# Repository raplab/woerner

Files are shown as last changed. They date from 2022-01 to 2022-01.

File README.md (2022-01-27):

# Wörner - Conventional Drill 
drilling and tapping machine control-code for a custom made electrical cabinet as upgrade of an old drill/milling-machine.
The controllino maxi automation acts as an SPS controlling various inputs and states - e.g. drilling, tapping and e-stop-mode.

## Requirements
- Controllino MAXI Automation https://www.controllino.com/product/controllino-maxi-automation/
- Eaton DE-1 (vfd) for motor control

# Documentation

## PIN Out
| Controllino Pin | Variable Name |  Input or Output |Cabinet Pin | Notes | 
|---|---|---|---|---|
| AI0 |  estop_pin |  INPUT |  - | read e-stop state, HIGH=ESTOP |
| AI1 |  contactor_pin | INPUT  | -  | read contactor state to determin if VFD has power  |
| AI2 |  vfd_state_pin |  INPUT | -  | read VFD state |
| AI3 |  cp_on_pin | INPUT  | -  |  spindle on |
| AI4 |  cp_off_pin | INPUT  | -  |  spindle off |
| AI5 |  cp_cw_pin | INPUT  | -  |  spindle direction clockwise |
| AI6 |  cp_ccw_pin | INPUT  | -  | spindle direction counterclockwise  |
| AI7 |  cp_mode_pin |  INPUT | -  | select between drilling or tapping mode  |
| AI9 |  w_topswitch_pin | INPUT  | -  | top switch for tapping mode (reverse spindle direction on HIGH) |
| AI10  |  w_bottomswitch_pin | INPUT  | -  |  bottom switch for tapping mode (reverse spindle direction on HIGH) |
| AI11  |  w_footswitch_pin |  INPUT | -  | foot switch for tapping mode (reverse spindle direction on HIGH)  |
| AI12  |  cp_speed_pin | INPUT  | -  |  analog input from 4.7k pot (0,1025) mapped to (0,255) vfd_speed_pin |
| AI13  |  tap_speed_pin | INPUT  | -  |  analog input from 4.7k pot (0,1025) mapped to (0,255) tap_speed_pin |
| DO0 |  cp_indicator_pin | OUTPUT  | -  | turn led on if spindle is on  |
| DO1 |  vfd_cw_pin | OUTPUT | -  |  turn spindle on in clockwise direction |
| DO2 |  vfd_ccw_pin | OUTPUT  | -  |  turn spindle on in counterclockwise direction  |
| DO3 |  ec_reset_pin | OUTPUT | -  |  led - high if reset is required |
| AO0 |  vfd_speed_pin | ANALOG OUTPUT  | | Analog out from 0-10V to control motor speed  |

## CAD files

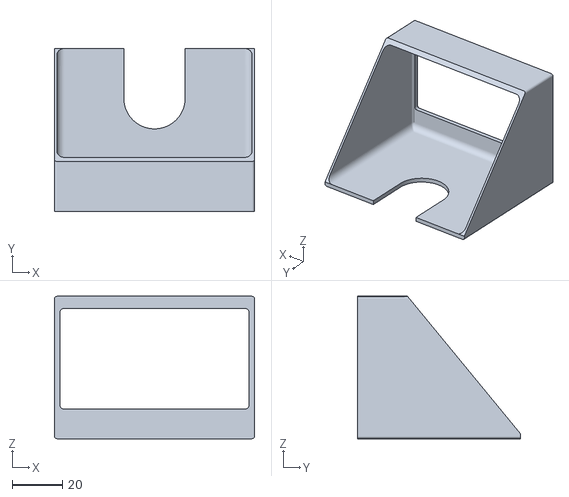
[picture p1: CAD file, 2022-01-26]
3d_prints/Wörner_Tacho_Housing.stl
80.0 x 65.2 x 57.0

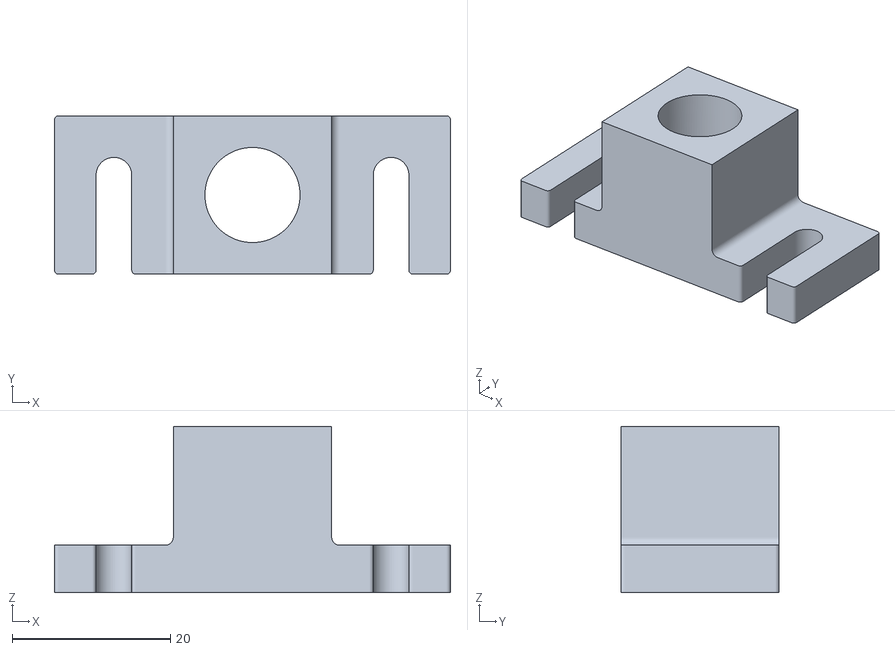
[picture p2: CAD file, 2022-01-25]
3d_prints/Sensor_Halter.stl
50.0 x 20.0 x 21.0

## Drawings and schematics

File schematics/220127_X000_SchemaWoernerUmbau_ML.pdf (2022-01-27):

-1F3

L3

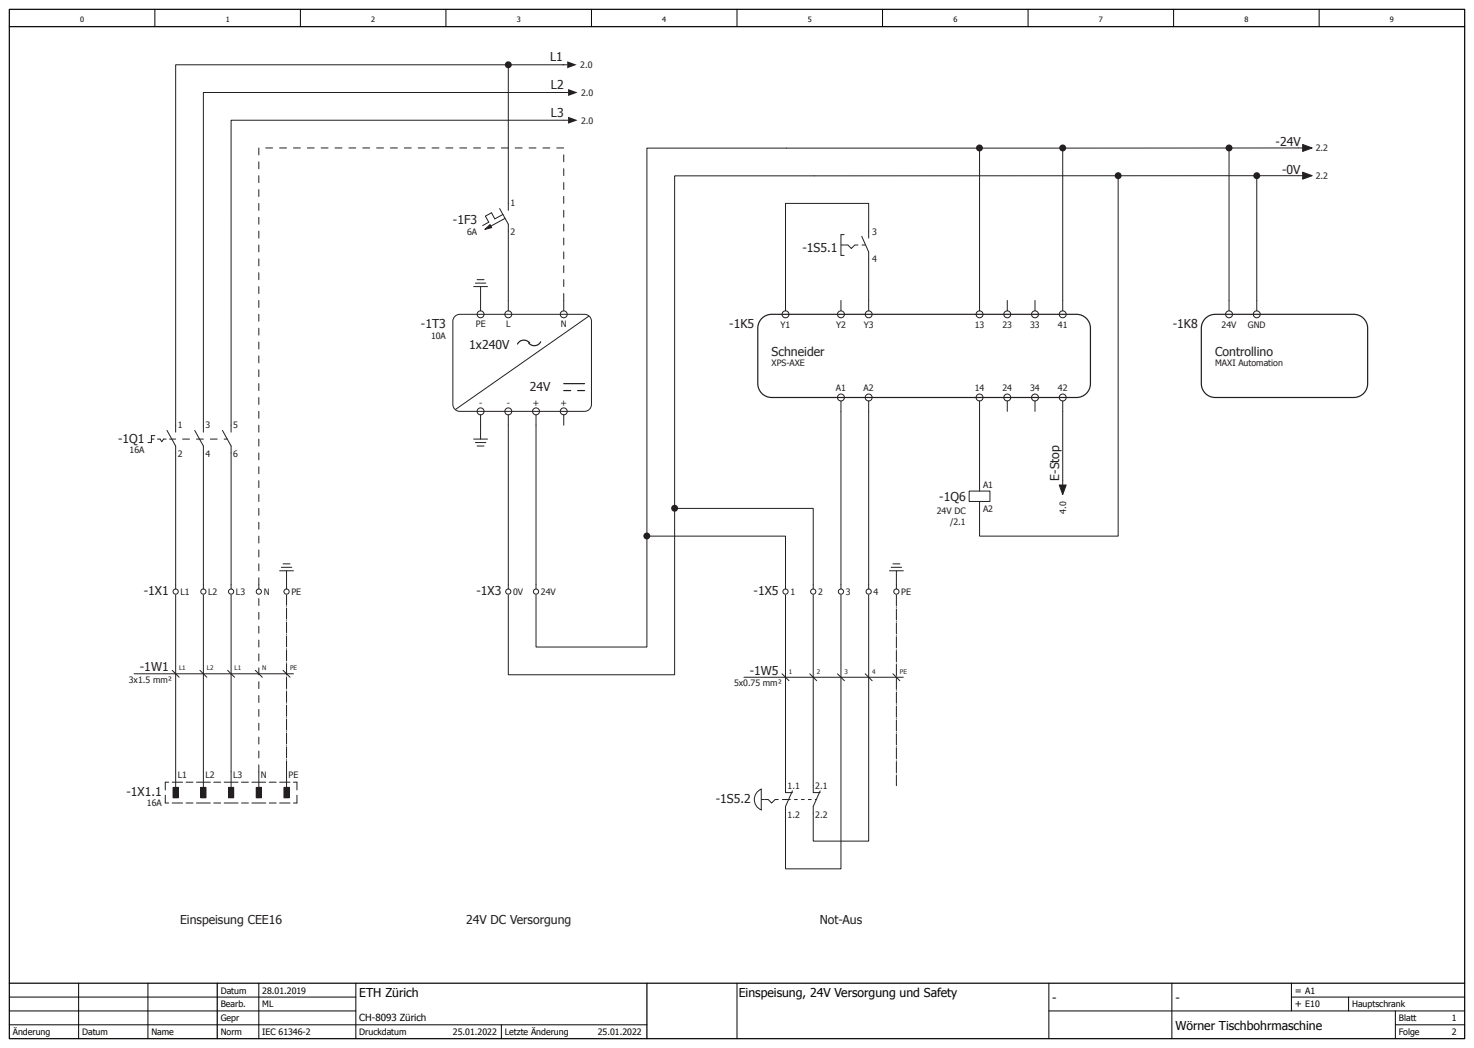
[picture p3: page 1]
Blatt Folge; Bearb.; Norm; Datum; Änderung; Letzte Änderung; Gepr; Druckdatum; Name; Hauptschrank; ETH Zürich; IEC 61346-2; Wörner Tischbohrmaschine CH-8093 Zürich; Schneider; XPS-AXE; 3x1.5 mm²; 5x0.75 mm²; Einspeisung CEE16; 24V DC Versorgung; Not-Aus; E-Stop 4.0; Controllino; MAXI Automation; GND

Einspeisung, 24V Versorgung und Safety

-2F1

-0V 1.8

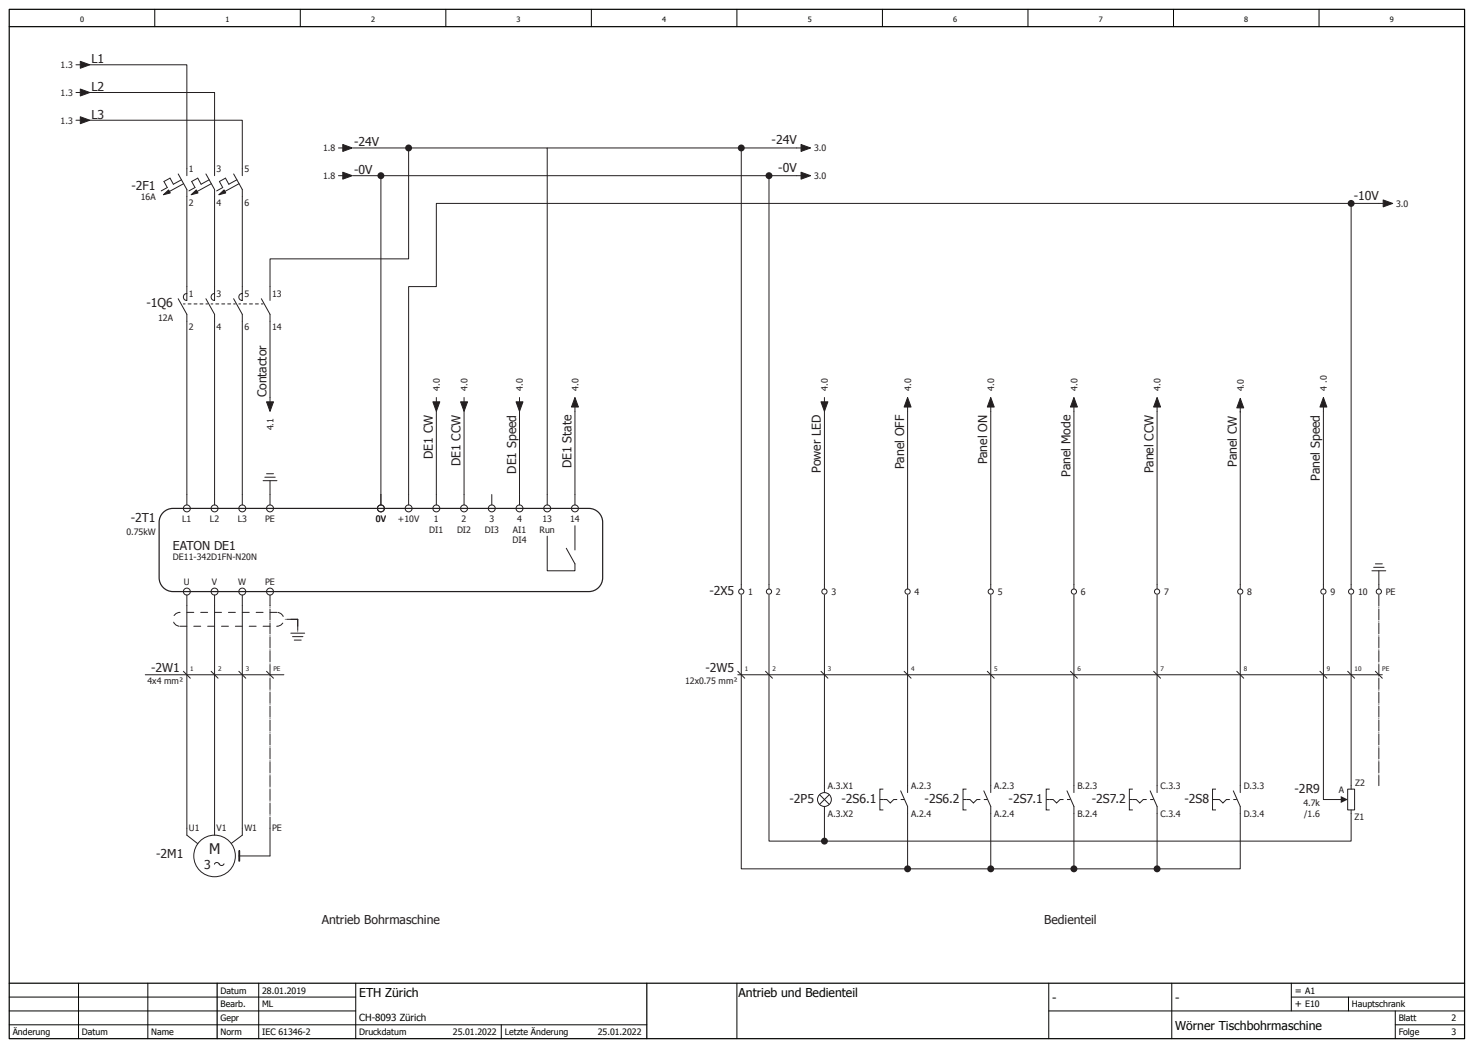
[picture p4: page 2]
EATON DE1; Run; 4x4 mm²; Antrieb Bohrmaschine; Bedienteil; DE1 CCW; DE1 Speed 4.0; DE1 State; Contactor; 12x0.75 mm²; 10 Panel OFF ⁴.0 Power LED ⁴.0; Panel ON ⁴.0; Panel Mode ⁴.0; Panel CCW ⁴.0; Panel CW ⁴.0; Panel Speed 4 .0

Antrieb und Bedienteil

-24V 2.5

-0V 2.5

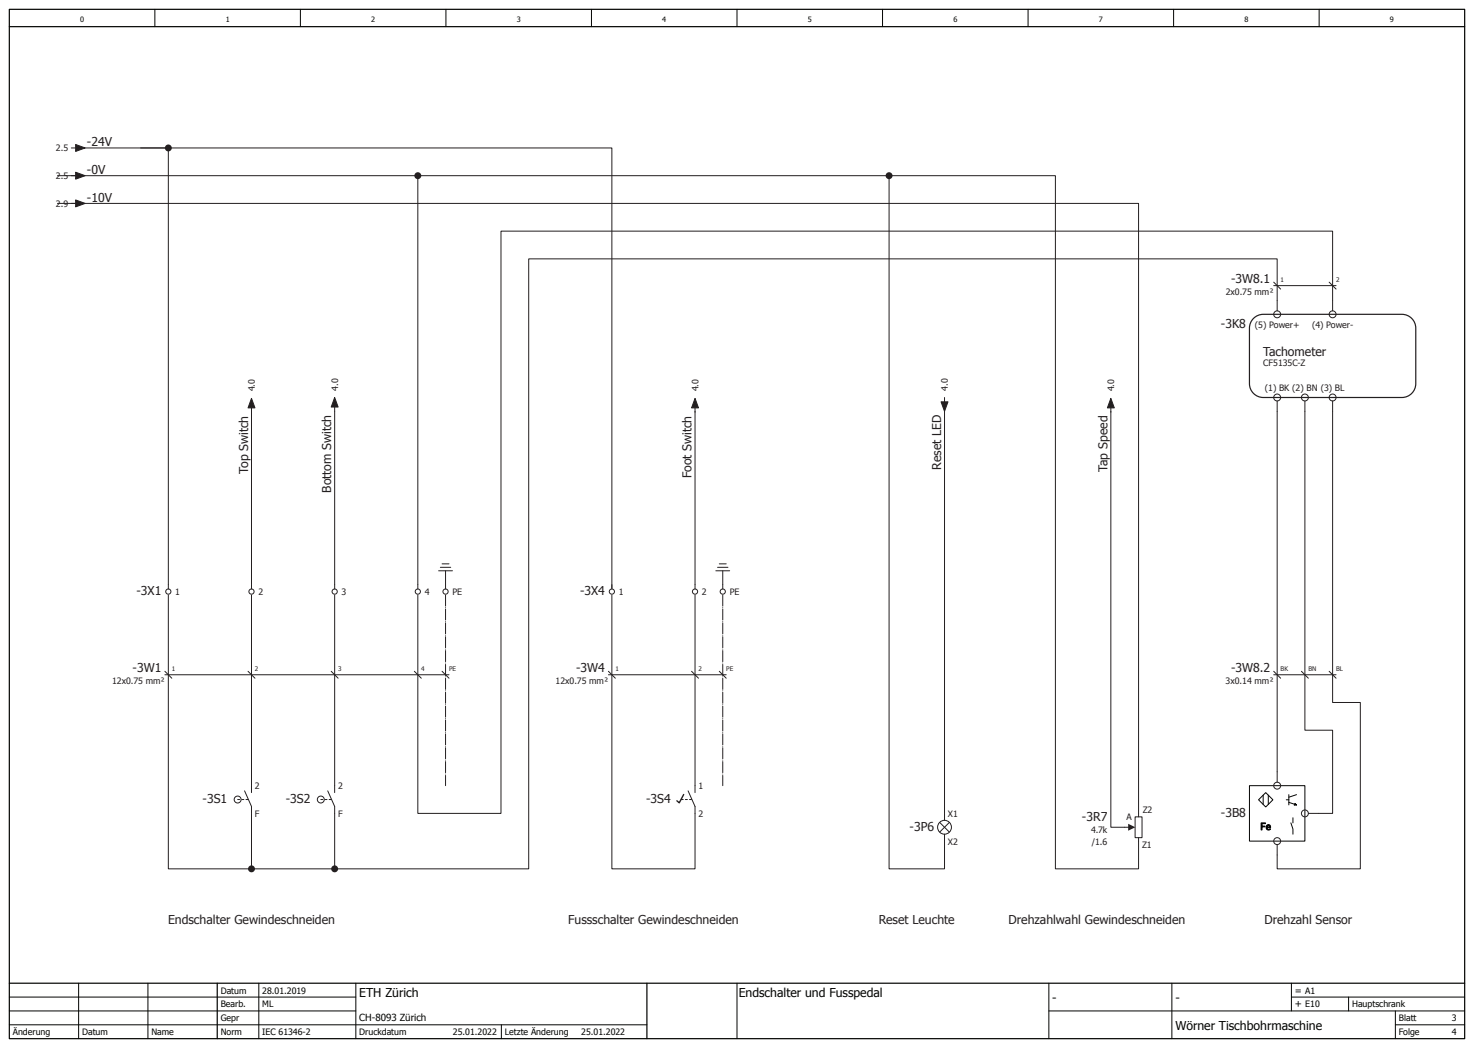
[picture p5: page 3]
Endschalter Gewindeschneiden; Fussschalter Gewindeschneiden; Reset Leuchte; Drehzahlwahl Gewindeschneiden; Drehzahl Sensor; 3 Top Switch ⁴.0; Bottom Switch ⁴.0; 12x0.75 mm²; 2 Foot Switch ⁴.0; Tap Speed 4.0; Reset LED; Tachometer; -3K8 (5) Power+; (4) Power-; 3x0.14 mm²; 2x0.75 mm²

Endschalter und Fusspedal

## Steuerung

AI0 | -
E-Stop

Analoger Eingang
-1K8

AI0

# E-Stop 2.0

AI1 | -
Contactor

Analoger Eingang
-1K8

AI1

## Contactor

2.0

AI2 | -
DE1 State

Analoger Eingang
-1K8

AI2

## DE1 State

2.0

AI3 | -
Panel ON

Analoger Eingang
-1K8

AI3

## Panel ON

2.0

AI4 | -
Panel OFF

Analoger Eingang
-1K8

AI4

## Panel OFF

2.0

AI5 | -
Panel CW

Analoger Eingang
-1K8

AI5

## Panel CW

2.0

AI6 | -
Panel CCW

Analoger Eingang
-1K8

AI6

## Panel CCW

2.0

AI7 | -
Panel Mode

Analoger Eingang
-1K8

AI7

## Panel Mode

2.0

AI12 | -
Panel Speed

Analoger Eingang (10V)
-1K8

AI12

# Panel Speed 2.0

AI9 | -
Top Switch

Analoger Eingang
-1K8

AI9

# Top Switch 2.0

AI10 | -
Bottom Switch

Analoger Eingang
-1K8

AI10

## Bottom Switch

2.0

AI11 | -
Foot Switch

Analoger Eingang
-1K8

AI11

## Foot Switch

2.0

DO0 | -
Power LED

Digitaler Ausgang

-1K8

DO0

DO2 | -
DE1 CCW

Digitaler Ausgang

-1K8

DO2

DO3 | -
Reset LED

Digitaler Ausgang

-1K8

DO3

AO11 | -
DE1 Speed

AnalogerAusgang

-1K8

AO11

# DE1 Speed 2.0

## Power LED

2.0

## DE1 CCW

2.0

## Reset LED

2.0

AI13 | -
Tap Speed

Analoger Eingang (10V)
-1K8

AI13

# Panel Speed 3.7

DO1 | -
DE1 CW

Digitaler Ausgang

-1K8

DO1

## DE1 CW

2.0

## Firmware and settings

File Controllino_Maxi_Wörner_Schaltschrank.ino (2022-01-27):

#include <SPI.h>
#include <Controllino.h>

//Emercency Stop - Input
#define estop_pin CONTROLLINO_AI0

//Contactor interupt - Input
#define contactor_pin CONTROLLINO_AI1

//Controlpanel - Input / Output
#define cp_on_pin CONTROLLINO_AI3
#define cp_off_pin CONTROLLINO_AI4
#define cp_cw_pin CONTROLLINO_AI5
#define cp_ccw_pin CONTROLLINO_AI6
#define cp_mode_pin CONTROLLINO_AI7 //mode selector -> drilling or tapping
#define cp_speed_pin CONTROLLINO_AI12 //analog input 4.7k pot
#define cp_indicator_pin CONTROLLINO_DO0 //output -> led

//Electrical Cabinet - Input / Output
#define ec_reset_led CONTROLLINO_DO3
#define tap_speed_pin CONTROLLINO_AI13 //analog input 4.7k pot setting the tapping speed

//Wörner endstops for tapping - Input
#define w_topswitch_pin CONTROLLINO_AI9
#define w_bottomswitch_pin CONTROLLINO_AI10
#define w_footswitch_pin CONTROLLINO_AI11

//Eaton DE1 Control- Input / Output
#define vfd_state_pin CONTROLLINO_AI2 //input
//#define vfd_run_pin CONTROLLINO_DO0
#define vfd_cw_pin CONTROLLINO_DO1
#define vfd_ccw_pin CONTROLLINO_DO2
#define vfd_speed_pin CONTROLLINO_AO0 // Analog out 0 - 0-10V

//Variables
int old_spindle_speed = 0;
int spindle_speed = 0;
int dir_change_delay = 10;
int fs_state = 0; //footswitch
int ts_state = 0; //topswitch
int bs_state = 0; //bootomswitch
int fs_last_state = 0; //footswitch
int ts_last_state = 0; //topswitch
int bs_last_state = 0; //bottomswich
String tspindle_dir = "CCW"; //CW or CCW

//STATES
enum m_mode {DRILL, TAP, ESTOP};
enum m_mode machine_mode;
enum m_state {ON, OFF};
enum m_state machine_state;
enum s_dir {CW, CCW, NONE};
enum s_dir spindle_direction;


void setup() {
  Serial.begin(19200);
  //e-stop, contactor, reset
  pinMode(estop_pin, INPUT);
  pinMode(contactor_pin, INPUT);
  pinMode(ec_reset_led, OUTPUT);

  //control panel
  pinMode(cp_on_pin, INPUT);
  pinMode(cp_off_pin, INPUT);
  pinMode(cp_cw_pin, INPUT);
  pinMode(cp_ccw_pin, INPUT);
  pinMode(cp_mode_pin, INPUT);
  pinMode(cp_speed_pin, INPUT);
  pinMode(cp_indicator_pin, OUTPUT);

  //wörner
  pinMode(w_topswitch_pin, INPUT);
  pinMode(w_bottomswitch_pin, INPUT);
  pinMode(w_footswitch_pin, INPUT);

  //eaton DE1
  pinMode(vfd_state_pin, INPUT);
  //pinMode(vfd_run_pin, OUTPUT);
  pinMode(vfd_cw_pin, OUTPUT);
  pinMode(vfd_ccw_pin, OUTPUT);
  pinMode(vfd_speed_pin, OUTPUT);

  //Waiting for ESTOP, CONTACTOR and VFD to signal all good!
  Serial.println("INIT...");
  while (digitalRead(estop_pin) == LOW && digitalRead(contactor_pin) == LOW && digitalRead(vfd_state_pin) == LOW) {
    Serial.println("waiting for e_stop, contactor and or vfd to start operation!");
    delay(250);
  }
  Serial.println("MACHINE READY!");
  
  //make sure spindle is off
  machine_state = OFF;
}

void loop() {
  check_mode();
  
  switch (machine_mode) {
    case DRILL:
      drilling_mode();
      break;
    case TAP:
      tapping_mode();
      break;
    case ESTOP:
      estop_mode();
      break;
    default:
      break;
  }
}

void check_mode() {
  //check drill, tap switch and estop and reset state
  if (digitalRead(estop_pin) == HIGH) {
    machine_mode = ESTOP;
  }
  if (digitalRead(estop_pin) == LOW && digitalRead(cp_mode_pin) == HIGH) {
    machine_mode = TAP;
  }
  if (digitalRead(estop_pin) == LOW &&  digitalRead(cp_mode_pin) == LOW) {
    machine_mode = DRILL;
  }
}

void run_machine() {
  check_onoff();
  //turn machine on or off
  switch (machine_state) {
    case ON:
      digitalWrite(cp_indicator_pin, HIGH);
      set_spindle_speed();
      if(machine_mode == DRILL){
        get_spindle_dir();
        set_spindle_dir();
      }
      if(machine_mode == TAP){
        if(spindle_direction == NONE){
          spindle_direction = CW;
        }
        get_tapping_dir();
        set_spindle_dir();
      }
      //digitalWrite(vfd_run_pin, HIGH);
      break;
    case OFF:
      digitalWrite(cp_indicator_pin, LOW);
      spindle_direction = NONE;
      set_spindle_dir();
      //digitalWrite(vfd_run_pin, LOW);
      break;
    default:
      break;
  }
}

void check_onoff() {
  //check input panel to see if the user turns the machine on or off
  if (digitalRead(cp_on_pin) == HIGH && digitalRead(cp_off_pin) == LOW) {
    machine_state = ON;
  }
  if (digitalRead(cp_on_pin) == LOW && digitalRead(cp_off_pin) == HIGH) {
    machine_state = OFF;
  }
}


void set_spindle_dir() {
  //set direction output pins
  switch (spindle_direction) {
    case CW:
      digitalWrite(vfd_ccw_pin, LOW);
      digitalWrite(vfd_cw_pin, HIGH);
      break;
    case CCW:
      digitalWrite(vfd_ccw_pin, HIGH);
      digitalWrite(vfd_cw_pin, LOW);
      break;
    case NONE:
      digitalWrite(vfd_cw_pin, LOW);
      digitalWrite(vfd_ccw_pin, LOW);
      break;
    default:
      break;
  }
}

void get_spindle_dir() {
  //get the current spindle direction
  if (digitalRead(cp_cw_pin) == LOW && digitalRead(cp_ccw_pin) == HIGH) {
    spindle_direction = CCW;
  }
  if (digitalRead(cp_cw_pin) == HIGH && digitalRead(cp_ccw_pin) == LOW) {
    spindle_direction = CW;
  }
  if (digitalRead(cp_cw_pin) == LOW && digitalRead(cp_ccw_pin) == LOW) {
    spindle_direction = NONE;
  }
}

void set_spindle_speed() {
  //set spindle speed acording to pot value
  if(machine_mode == DRILL){
    spindle_speed = analogRead(cp_speed_pin);;
  }
  if(machine_mode == TAP){
    spindle_speed = analogRead(tap_speed_pin);;
  }
  int speed_value = int(map(spindle_speed, 0, 1025, 30, 255));
  analogWrite(vfd_speed_pin, speed_value);
}

void get_tapping_dir() {
  //invert spindle direction when either top or bottom endstop are pressed
  bs_state = digitalRead(w_bottomswitch_pin);
  ts_state = digitalRead(w_topswitch_pin);
  fs_state = digitalRead(w_footswitch_pin);
  //check bottom switch
  if (bs_state != bs_last_state) {
    if (bs_state == HIGH) {
      spindle_direction = CCW;
    }
  }
  //check top switch
  if (ts_state != ts_last_state) {
    if (ts_state == HIGH) {
      spindle_direction = CW;
    }
  }
  //check foot switch
  if (fs_state != fs_last_state) {
    if (fs_state == HIGH && ts_state == LOW && bs_state == LOW) {
      spindle_direction = CCW;
    }
  }

  fs_last_state = fs_state;
  bs_last_state = bs_state;
  ts_last_state = ts_state;
}

void drilling_mode() {
  Serial.println("DRILLING MODE");
  machine_state = OFF;
  while (true) {
    check_mode();
    run_machine();
    if (machine_mode != DRILL) {
      break;
    }
  }
}

void tapping_mode() {
  Serial.println("TAPPING MODE");
  machine_state = OFF;
  while (true) {
    check_mode();
    run_machine();
    if (machine_mode != TAP) {
      break;
    }
  }
}

void estop_mode() {
  Serial.println("ESTOP MODE");
  digitalWrite(ec_reset_led, HIGH);
  digitalWrite(cp_indicator_pin, LOW);

  while (true) { 
    if (digitalRead(estop_pin) == LOW && digitalRead(contactor_pin) == HIGH) {
      Serial.println("RESET PRESSED!");
      digitalWrite(ec_reset_led, LOW);
      machine_state = OFF;
      break;
    }
  }
}
